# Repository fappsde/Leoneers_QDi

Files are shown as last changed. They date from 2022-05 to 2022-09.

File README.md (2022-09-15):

# Future Engineers - Leoneers_QDi - Deutschlandfinale

Dieses Repository bietet Einblicke in den Weiterentwicklungsprozess unseres autonom fahrenden Roboterautos nach unserem Vorentscheid in Dortmund, welches wir im Rahmen der Future Engineers Category der World Robot Olympiad (WRO) konzipiert und programmiert haben. 
Die unveränderte Dokumentation des Vorentscheids ist diesem [Branch](https://github.com/fappsde/Leoneers_QDi/blob/Vorentscheid_Dortmund/README.md) zu finden.

# Inhalt
  * Bilder
  * Programmcode
    * Module des Codes
    * Zusammenhang der Module und der elektromechatronischen Komponenten
    * Prozess des Erstellens, Kompilierens und Hochladens auf die Steuergeräte
  * Technische Zeichnungen
  * Video
  
# Einleitung
Wir, dass sind Felix und Philipp aus Aachen, haben seit der 5. Klasse jährlich an der WRO teilgenommen. Dementsprechend war die WRO eine Konstante in unserer Schulzeit, auf die wir uns jedes Jahr aufs neue freuten. Eigentlich wollten wir im Jahr 2020 das letzte Mal vor unserem Abitur 2021 in der Football Category antreten. Daraus wurde leider nichts. Umso größer war die Freude als wir feststellten, dass wir dieses Jahr ein aller letztes Mal die Möglichkeit haben an der WRO teilnehmen zu können. Zwar stellten wir fest, dass die Football Category, welche uns die vergangenen Jahre immer viel Spaß bereitete, nicht mehr ausgetragen wird, aber genau so spannend und interessant erschienen uns die neuen Kategorien der WRO. 
Da uns beide die Thematik der zukünftigen Mobilität und das autonome Fahren interessiert, entschieden wir uns dazu an der Future Category teilzunehmen, und ein autonomfahrendes Auto zu konzipieren.

## Anfängliche Entscheidungen

Nachdem wir die Entscheidung getroffen hatten, dass wir teilnehmen wollen, kam die Frage auf mit welchem Roboter System wir die Herausforderung des Autonomenfahrens meistern wollen? In der Vergangenheit arbeiteten wir immer gerne mit dem EV3 und Lego Technik. Jedoch stießen wir insbesondere die Programmierung betreffend mit der EV3 eigenen Programmiersprache auf Grenzen. Aus diesem Grund entschlossen wir uns dazu eine neue Herausforderung anzunehmen, und die EV3 Welt hinter uns zu lassen. Mit dieser Entscheidung dem Mindstorms Kosmos den Rücken zu zukehren, waren wir nun allerdings mit der Frage konfrontiert für welches der zahlreichen Robotersysteme, welche auf dem Markt erhältlich sind, wir uns entscheiden wollten.

Zunächst überlegten wir uns das Roboterauto von Grund auf selbst mittels CAD und additiver Herstellung zu konstruieren. Jedoch wurde uns schnell klar, dass dies zeitlich neben dem Studium leider nicht möglich gewesen wäre. Deshalb wählten wir ein altes ferngesteuertes Auto als Chassis unseres ersten Roboterautos für die Teilnahme am Vorentscheid. Als EV3 Stein Ersatz arbeiteten wir von nun an mit einem Raspberry Pi CM4. Des Weiteren verfügte das erste Auto über zwei Raspberry Pi Kameras, welche wir für das autonome Fahren und das Erkennen der Hindernisse verwendeten. Damit der Antriebs- und der Servomotor vernünftig vom Raspberry Pi angesteuert werden können, mussten wir feststellen, dass ein ESP 32 Mikrocontroller notwendig war, da das PWM (Pulsweitenmodulation) Signal ansonsten nicht konstant gewesen wäre, was ein Zittern des Servomotors verursacht hätte. Mit dieser technischen Ausstattung fuhren wir zum Vorentscheid nach Dortmund.

## Vorentscheid Dortmund

Aufgrund unserer zahlreichen Teilnahmen seit der 5. Klasse an der WRO wissen wir, dass der eigentliche Wettbewerbstag immer etwas ganz besonderes ist. Nicht nur, weil es ein schönes Ereignis in einer uns fremden Stadt ist, sondern auch, weil an diesem Tag die intensive Arbeit der letzten Wochen und Monate auf die Probe gestellt. Des Öfteren fuhren wir mit einem sehr guten Gefühl zum Wettbewerb, und mussten dann leider feststellen, dass wir uns getäuscht hatten, da der Roboter auf einmal nicht mehr das machte, was er sollte bspw. aufgrund der örtlichen Gegebenheiten, welche die Sensorik anders beeinflusst als bei der Vorbereitung. Dementsprechend lernten wir über die Jahre mit Überraschungen am Wettbewerbstag umgehen zu können. 
Ein ähnliches Erlebnis hatten wir auch bei unserem Vorentscheid in Dortmund im Juni. Zuhause und vor den Wettbewerbsdurchläufen vor Ort alles perfekt läuft. Doch dann kommt der entscheidende Durchlauf, wo unser Auto auf einmal nach der ersten Kurve an der Bande hängen blieb, was in diesem Augenblick natürlich sehr ärgerlich und frustrierend ist. Aber auch das gehört zur WRO dazu.

Dennoch hatten wir das Glück, dass wir uns als 1. Platz für das Deutschlandfinale qualifizieren konnten. Wir freuen uns sehr auf diese neue Herausforderung, denn in Dortmund stellten wir die folgenden Probleme fest, die es zu lösen galt:
 * Zu großer Wenderadius, wodurch das Auto die Kurven zu groß fuhr und auch nicht flexibel genug den Hindernissen ausweichen konnte.
 * Die Bandenerkennung, die wir mittels einer Bilderkennung implementierten, war vor Ort fehleranfällig, da das Bild der Kamera überbelichtet war, sodass  die schwarze Bande nicht mehr erkannt werden konnte. 

## Umbau des Roboterautos
Mit den in Dortmund festgestellten Problemen begann für uns zu Hause wieder die Arbeit, diese Probleme zu beheben. Dadurch, dass der Wenderadius zu groß war und auch an dem alten Modell nicht mehr vergrößert werden konnte, mussten wir um diesen zu verkleinern noch eine Hinterradlenkung einbauen. Wir entschieden uns einen zweiten Prototypen zu entwickeln, um das Auto, was bereits funktionierte auch wenn nicht perfekt, nicht zu demontieren, um so ggf. auf ein Backup zurückgreifen zu können. 

### Doppelachslenkung

Damit wir die Hinterradlenkung verbauen konnten, mussten wir zunächst die aktuelle Bodenplatte des Roboterautos neu konstruieren, um jeweils vorne und hinten eine Lenkeinheit verbauen zu können. Außerdem musste die Position des Motors geändert werden und ein weiterer Servomotor musste verbaut werden. Zunächst fertigten wir eine technische Zeichnung auf Papier an um diese anschließen in das CAM Programm zu übertragen. Dadurch, dass wir die neue Bodenplatte aus Aluminium frästen, waren diese Arbeitsschritte notwendig. 

### Elektromechanische Komponenten und Platinendesign 

Eine weitere Umbaumaßnahme ging mit dem Design einer eigenen Platine einher. Damit entstand wohl auch der optisch größte Unterschied vom neuen Modell zum alten, denn dank der Platine verschwand der auffällige Kabelbaum. Nicht nur optisch verschönert die Platine das Auto, sondern sie verfügt über jeweils zwei verbaute Rasberry Pi CM4 Module und ESP32 über mehr Rechenleistung und spart gleichzeitig noch Gewicht ein.

Beim alten Modell ist der verbaute ESP32 regelmäßig abgestürzt. Es lag die Vermutung nahe, dass das Abstürzen durch zu wenig Rechenleistung verursacht wurde, sodass das Ansteuern der Lenkung und der Beleuchtung zu viel für einen ESP war. Deshalb designten wir die Platine so, dass die Platine nun Platz für zwei ESP32 bietet. Der eine ESP übernimmt die Ansteuerung der Doppelachslenkung und der zweite ESP ist dafür gedacht die nicht unbedingt notwendigen Spielereien, wie das Bremslicht anzusteuern. So konnten wir bis dato Abstürze des ESP‘s verhindern.

In unserem alten Modell verbauten wir zwei Kameras, die jeweils einen Blickwinkel von 60 Grad, so erzielten wir einen Blickwinkel von 120 Grad. Allerdings mussten wir im Vorentscheid feststellen, dass dies insbesondere beim Vorbeifahren an den Hindernissen zu wenig war. Daher war  der nächste Schritt naheliegend eine dritte Kamera zu verbauen, um einen größeren Öffnungswinkel von 180 Grad zu erhalten. Allerdings begrenzte ein Rasberry Pi uns daran, denn an einen Rasberry Pi können lediglich nur zwei Kameras angeschlossen werden. Da für uns klar war, dass wir drei Kameras verbauen wollten, mussten wir noch einen zweiten Rasberry Pi anschließen, was in dem Design der Platine ebenfalls berücksichtigt wurde.

## Autonomes Fahren und Hinderniserkennung

Bereits vor dem Vorentscheid war unsere erste Idee, die wir für die Orientierung auf dem Spielfeld verfolgten, die Verwendung von Lidar Sensoren, welche vorne und jeweils an den Seiten des Autos verbaut wurden. Lidar Sensoren werden bereits für das autonome Fahren in Kraftfahrzeuge verbaut, da diese ein Abbild der Umgebung erzeugen können. Dadurch, dass die Lidar Sensoren mit Infrarotlicht arbeiten, stellten wir fest, dass die damaligen Lidarsensoren mit der schwarzen Bande des Spielfeldes nicht kompatibel war, weshalb wir die Idee der Lidar Sensoren verwerfen mussten.
Die Alternative auf die wir uns dann konzentrierten, war die Verwendung der Kameras. Wir verwendeten zwei Kameras. Mithilfe der Kameras gelang es uns die Banden und die Hindernisse zu erkennen. Dementsprechend fuhr die erste Version mithilfe von Bilderkennungsalgorithmen autonom.

Beim Vorentscheid wurde uns jedoch klar, dass die nur die Verwendung der Kameras auch ihre Schwächen mit sich brachte. Denn das Problem war, dass die Bande in bestimmten Situationen zu reflektierend wirkte und so auf der Kamera nicht mehr schwarz sondern weiß erschien. 
Uns war daher klar, dass wir die Problematik der Überbelichtung umgehen wollten und uns beim autonomen Fahren nicht mehr auf die Kameras verlassen wollten. Dies führte dazu, dass wir noch einmal unsere erste Idee, die Verwendung von Lidar Sensoren, aufgriffen. Dieses mal wurden wir auch nach einem Lidar Sensor fündig, der sich durch die schwarze Bande nicht beirren lässt. Statt mehreren Lidar Sensoren, die an den jeweiligen Seiten verbaut werden, dreht sich der neue Lidar permanent im Kreis, sodass wir nicht mehrere verbauen musste. 

Der schöne Vorteil an dem funktionierenden Lidar im Vergleich zu der Verwendung der Kameras, ist, dass wir so wesentlich besser die Banden erkennen können und das auch schon aus einer gewissen Distanz. Die Entfernungen, welche der Lidar misst, lassen sich anschließend in einer Karte kartographieren. Da wir bei der alten Version auch nicht wussten, wo wir uns auf dem Spielfeld befanden, haben wir noch eine Positionskamera verbaut. Die Positionskamera begegnet uns im Alltag täglich, wenn man eine Computer Maus benutzt. Die gleiche Technik machen wir uns zu Nutze, sodass mit den Winkelinformationen des Gyro Sensors und der Positionskamera die genaue Position des Autos in der Karte, die das Spielfeld darstellt eintragen können. Das ermöglicht es uns die Banden nicht anzufahren. 

Für das Erkennen der Hindernisse im Hindernisrennen ist die Verwendung der Kameras aber weiterhin notwendig, da wir die Farben ermittelt werden müssen, was der Lidar nicht kann. 

## Herausforderungen im Entwicklungsprozess

Nicht nur unser Auto muss die Hindernisse im Rennen meistern, sondern auch wir sind in der Entwicklung auf das ein oder andere Hindernis gestoßen. Aus unseren Lego Mindstorms Zeiten kannten wir es bereits uns mit unerwartet auftretenden Fehlen zu befassen, die nicht nur Zeit sondern auch Nerven kosten. So waren wir bspw. in der Wettbewerbswoche einmal an dem Punkt, dass die Kameras auf einmal nicht mehr funktionieren wollten. Dann begann eine lange Fehlersuchnacht, bis wir die Ursache, Lötzinnreste auf der Platine, die einen Kurzschluss verursachten, auffinden konnten. Ein ähnlich ärgerliches Problem ereignete sich einen Tag vor unser Abfahrt zum Wettbewerb nach Chemnitz und zwar brannte einer der Servomotoren durch. Das Problem war dann in dieser kurzen Zeit einen neuen Servo zu bekommen, den dann wieder zu verbauen und mit dem Programm in Einklang zu bringen.

Eine WRO Teilnahme ohne Harausforderungen wäre ja auch langweilig:)

# Übersicht der technischen Komponenten

* 2 x Raspberry Pi CM4
* 2 x ESP 32 Mikrocontroller
* 3 x Raspberry Pi Kamera
* Gyro Sensor
* Lidar Sensor
* Positionskamera

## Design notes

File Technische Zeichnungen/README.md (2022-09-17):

# Technische Zeichnungen

Als Chassis entschieden wir uns dazu ein altes ferngesteuertes Auto zu verweden. Um den Raspberry Pi und die anderen Komponenten mit diesem Chassis verbinden zu können, mussten wir zunächst mit CAD Halterungen erstellen, welche wir anschließend mit unserem 3D-Drucker druckten.

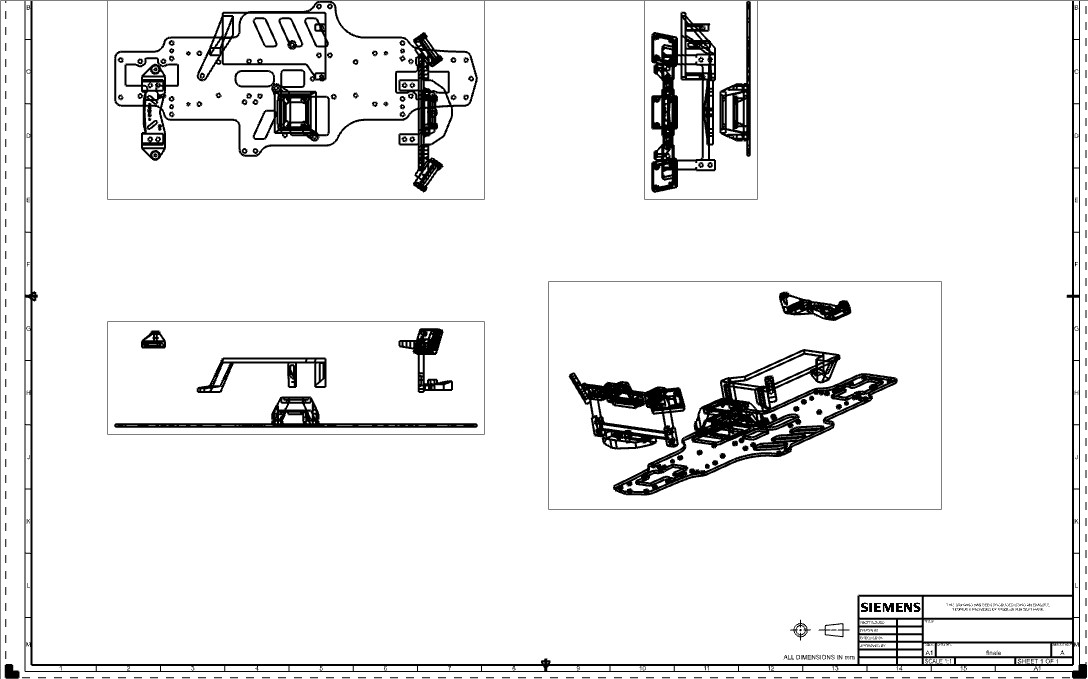
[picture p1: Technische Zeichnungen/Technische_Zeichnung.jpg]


# Schaltpläne für die Hauptplatine
Die Platine für die zweite Genration wurde von uns mit dem Programm EAGLE (Einfach Anzuwendender Grafischer Layout Editor) erstellt. Dazu haben wir zuerst alle gewünschten Komponenten gewählt und einen passenden Schaltplan mit diesen erstellt. Mit diesem Schaltplan kann man anschließend ein Layout der Komponenten erstellen, wie diese später auf der Platine platziert werden sollen. Ziel war es, auf so wenig wie möglich PLatz alle Bauteile zu platzieren. Schlussendlich war es uns möglich mit 4 Lagen und einer Größe von 20cm x 7.5cm alle Komponenten unterzubringen. Damit ist die PLatine nur knapp größer als das Raspberry Pi CM4 IO Board, welches wir in der ersten Generation verwendet haben. Dennoch ist die doppelte Rechenleistung auf dieser, inklusive ESP-23ige und Steckern, untergebracht. Für diese haben wir bei der In der ersten Generation noch eine extra Platine und viele Kabel gebraucht.

Die gesamte Entwicklung und Inbetriebnahme der Platine, sowie die dazugehörigen Aufgaben wurden ohne externe Hilfe in unserem Team durchgeführt. Die Bestückung der SMD-Bauteile wurde freundlicherweise Maschinell bei der PicoLAS-GmbH durchgeführt.
Selbes gilt auch für die Entwicklung des gefrästen Chassis.

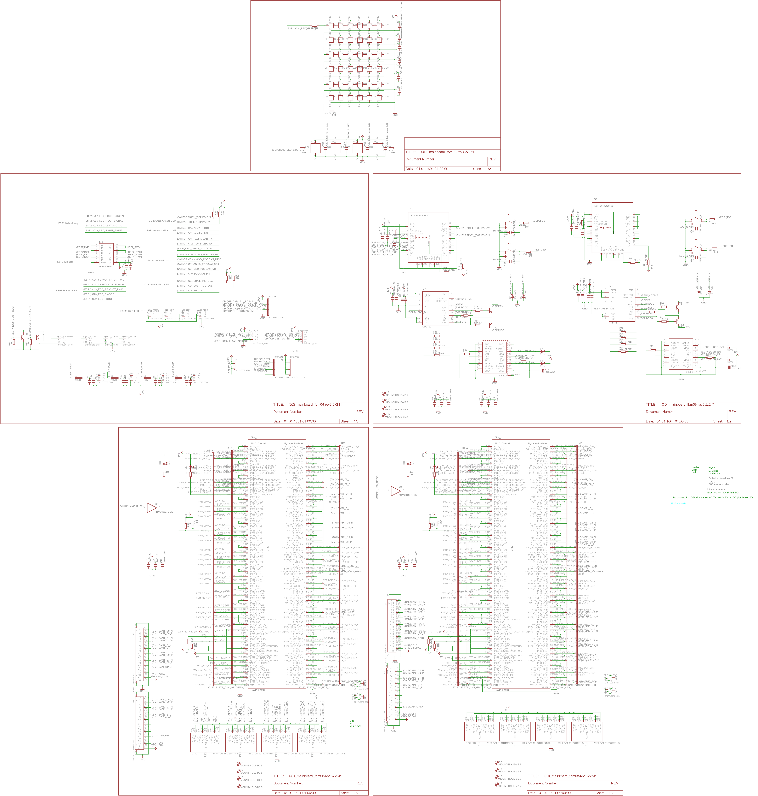
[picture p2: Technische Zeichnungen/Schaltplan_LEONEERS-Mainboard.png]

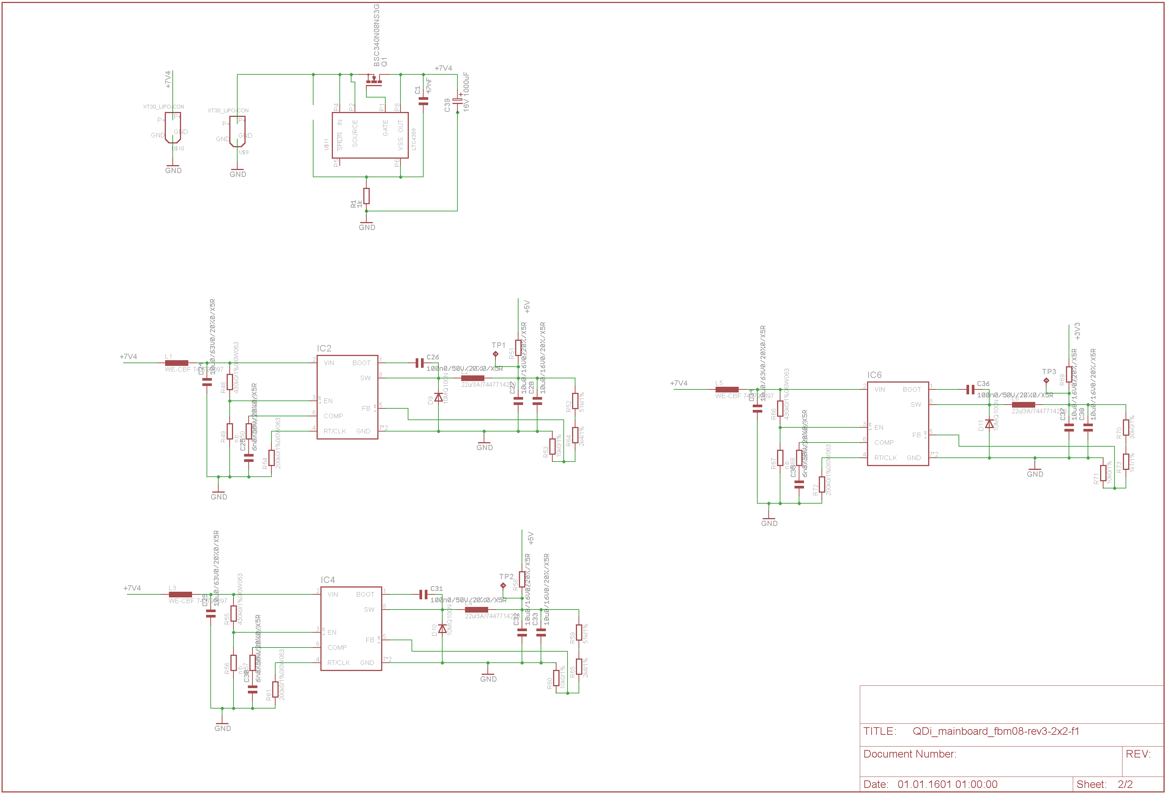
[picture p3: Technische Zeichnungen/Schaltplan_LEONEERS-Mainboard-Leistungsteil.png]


# Layout der Hauptplatine

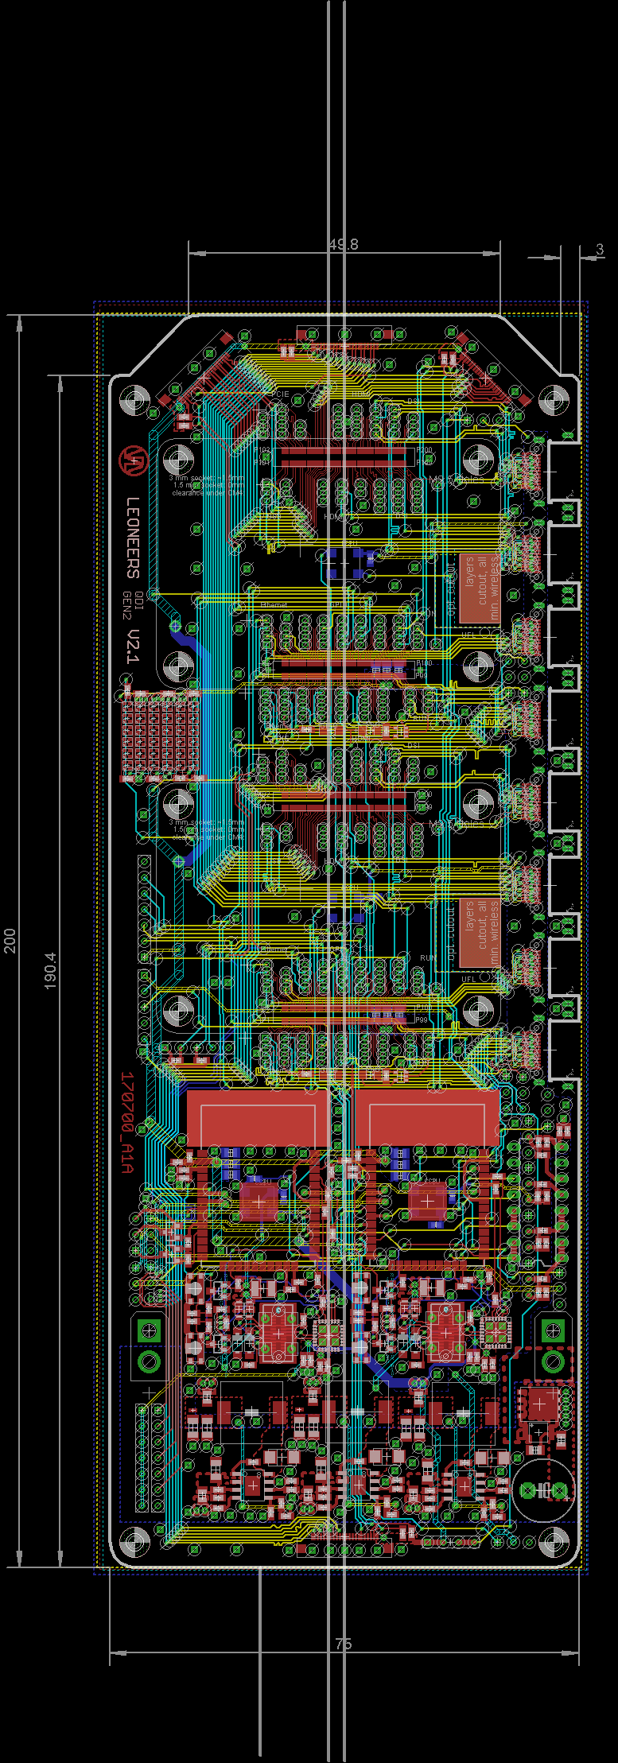
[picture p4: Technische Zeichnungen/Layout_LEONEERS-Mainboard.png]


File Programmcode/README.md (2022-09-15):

# Programmstruktur
Im Wesentlichen lässt sich unsere Programmstruktur in zwei Teile seperieren, einerseits das Programm für die ESP und andererseits die Programme der beiden Raspberry Pi's.  
Als Schnittstelle zwischen dem Antrieb des Roboterautos und dem einen dafür zuständigen Raspberry Pi fungiert ein ESP, welcher mittels Arduino programmiert wurde. Die Raspberry Pi's programmierten wir mit C und C++, da wir im Entwicklungsprozess feststellten, dass Python sich auf die Geschwindigkeit negativ ausgewirkt hätte. 

## Module des Codes

Unser Code lässt sich in mehrere Teile unterteilen, dieser verfügt unter anderem über ein Hauptprogramm. Des Weiteren über ein Programm, welches die Kameras auswertet und die Daten permanent an das Hauptprogramm übermittelt. Außerdem gibt es noch ein Programm, das den Gyro Sensor ausließt. Diese Teile waren bereits der ersten Version. Bei unserer jetzigen Version sind noch die Programmteile hinzugekommen, die den Lidar und die Positionskamera auswerten und das Kartographieren der Karte übernehmen. Das Hauptprogramm, welches auf dem Raspberry Pi läuft, dient dann dazu alle Daten zusammen fließen zu lassen und die Geschwindigkeit und Richtung des Autos vorzugeben.

## Zusammenhang der Module und der elektromechatronischen Komponenten
Damit die Motoren jedoch angesteuert werden können, übermittelt das Hauptprogramm zunächst die Informationen an den einen ESP, der dann den Antriebs- und die Servomotoren ansteuert. Dementsprechend lässt sich sagen, dass der eine ESP die Aufgabe erfüllt die Motoren anzusteuern.

## Erstellen/Kompilieren/Hochladen
Die ESP's werden über Arduino kompiliert und das Programm anschließend mittels USB hochgeladen. Auf den Raspberry Pi's werden die Programme direkt geschrieben und beim Power Up gestartet.

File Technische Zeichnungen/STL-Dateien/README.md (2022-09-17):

Hier haben wir alle STL- Dateien von den von uns erstellten 3D-Modellen gesammelt.
Auf https://1drv.ms/f/s!Ajk7HkkcY5YIkIYCL9fZXsYnURJLaA OneDrive können die Dateien als 3D Vorschau angezeigt werden.

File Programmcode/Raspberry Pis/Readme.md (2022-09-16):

Die Raspberry Pis werden mit mehreren verschiedenen Klassen gesteuert, welche jeweils einem Sensortyp bzw einer Funktionsgruppe zugeordnet sind. In der Mainloop-Klasse fließen die Daten zusammer und werden zu fahrbefehlen umgewandelt. Zudem werden hier die einzelnen Sensoren gesteuert, die jeweils gleichzeitig und asynchron laufen.

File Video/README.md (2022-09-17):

Hier gelangen Sie zu unserem [neuem Youtube Video](https://youtu.be/PLEGRZtfeYY) und hier zum [alten Youtube Video](https://youtu.be/amUso_nRZ14).

(Beim Rendern des neuen Videos ist leider am Ende ein Fehler unterlaufen)

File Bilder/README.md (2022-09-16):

Hier sehen Sie unseren Roboter
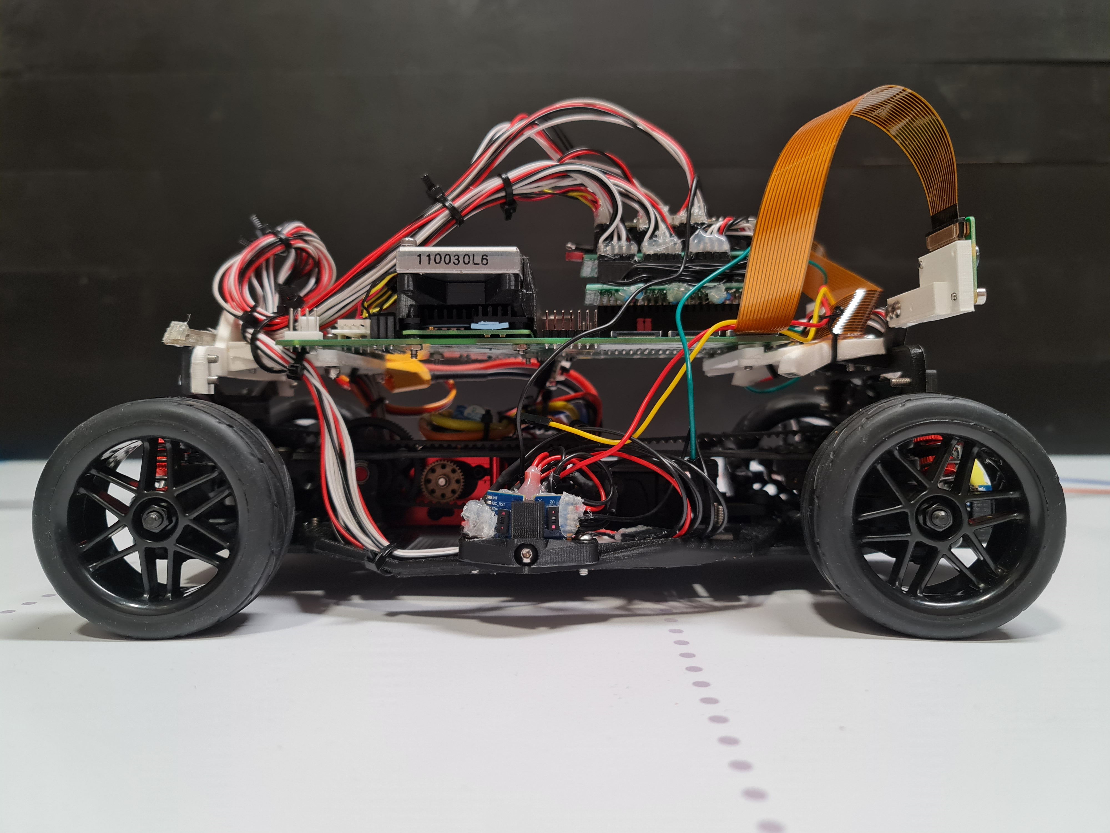
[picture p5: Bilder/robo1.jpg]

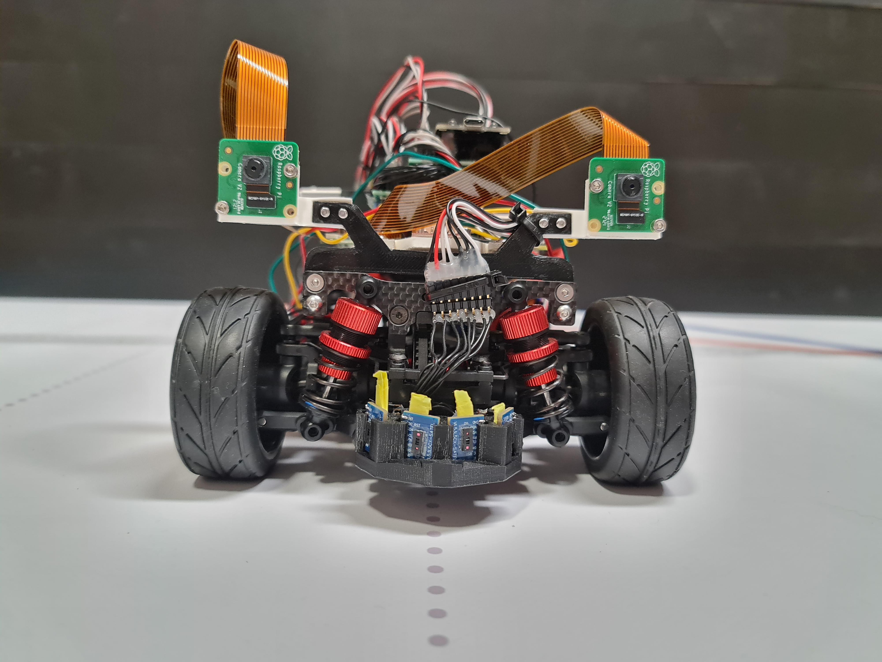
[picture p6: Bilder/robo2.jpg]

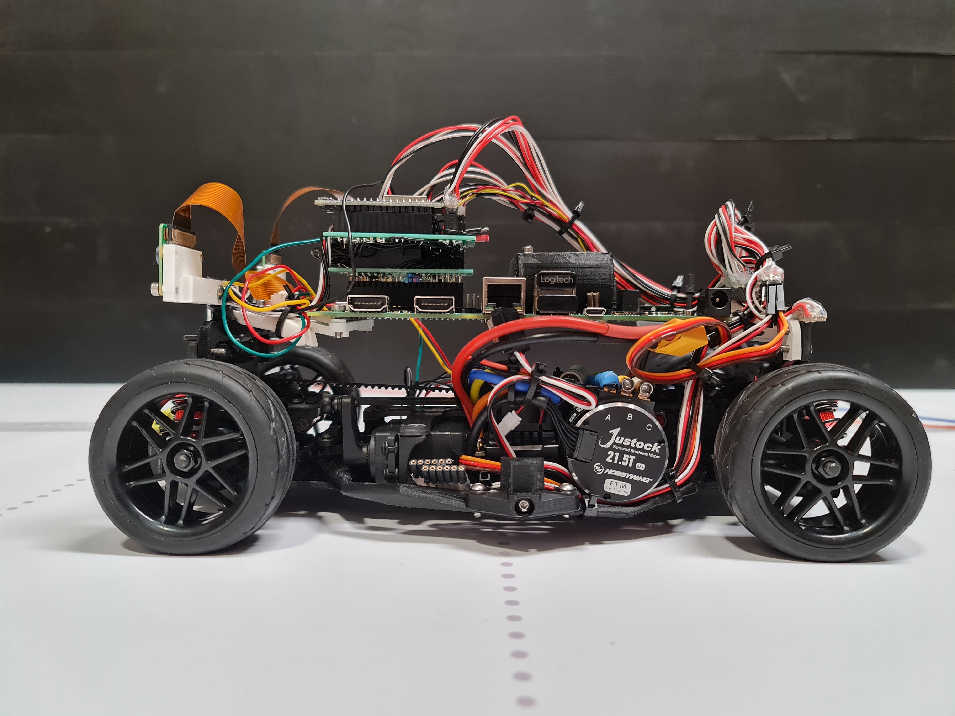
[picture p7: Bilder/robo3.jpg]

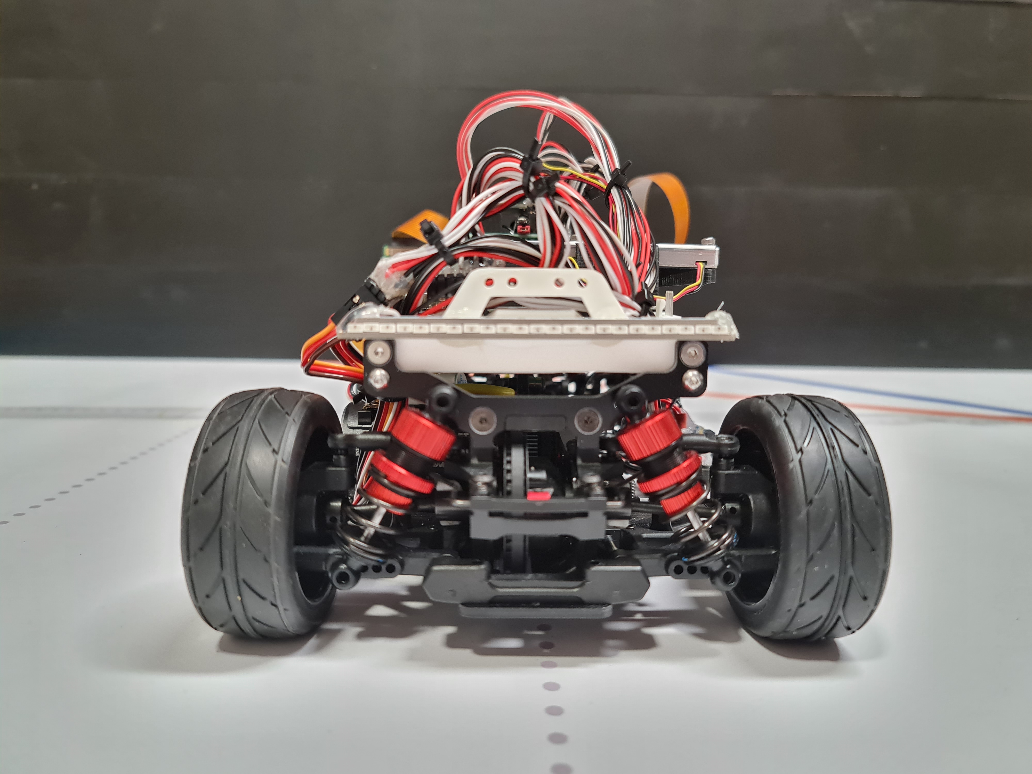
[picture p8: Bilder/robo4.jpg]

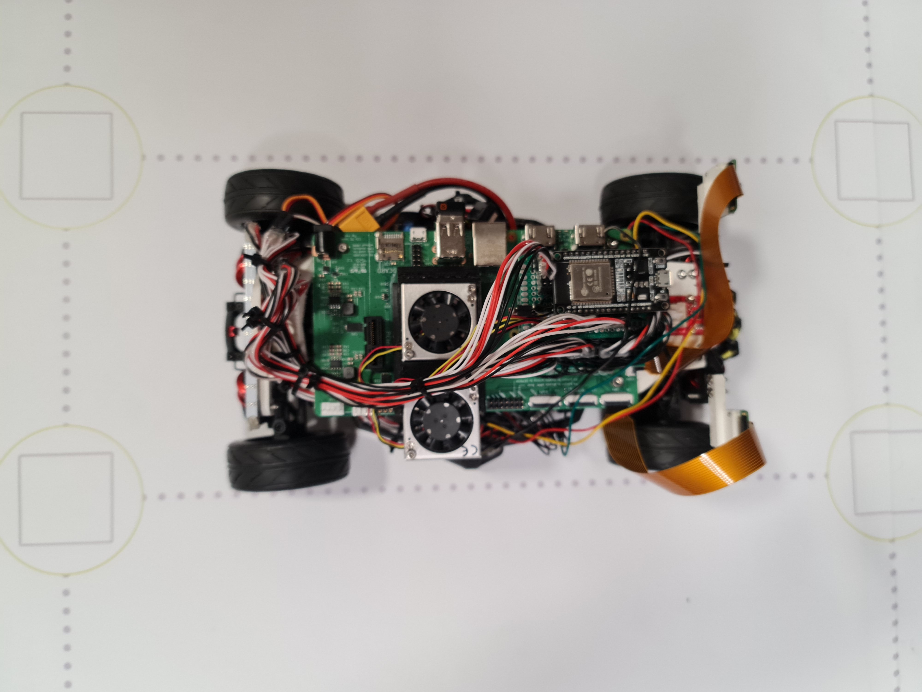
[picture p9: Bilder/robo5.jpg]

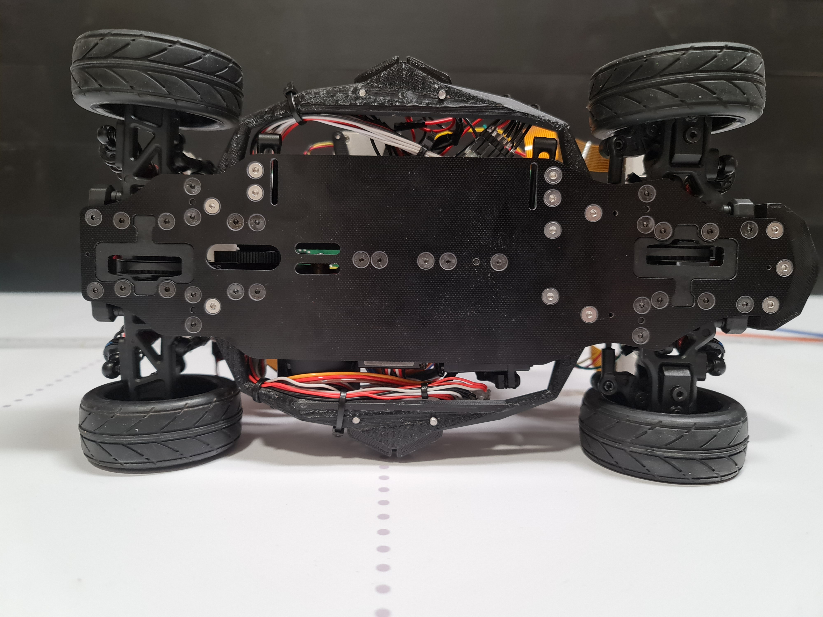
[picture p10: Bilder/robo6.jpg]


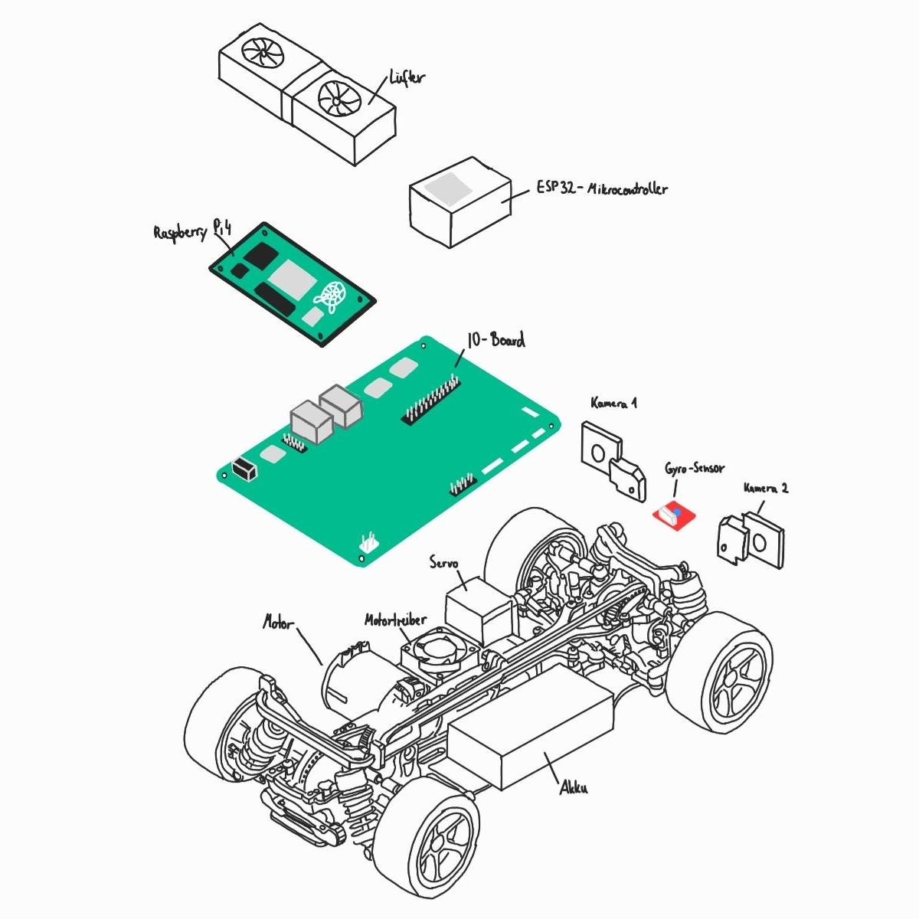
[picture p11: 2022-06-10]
Technische Zeichnungen/robo7.jpg

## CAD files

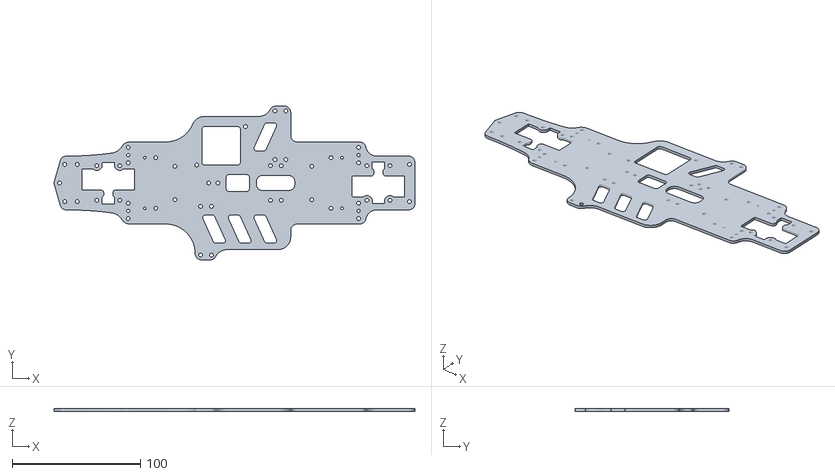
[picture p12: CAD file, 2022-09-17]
Technische Zeichnungen/STL-Dateien/chassis_tfl03_fbm04.stl
281.6 x 120.0 x 2.00

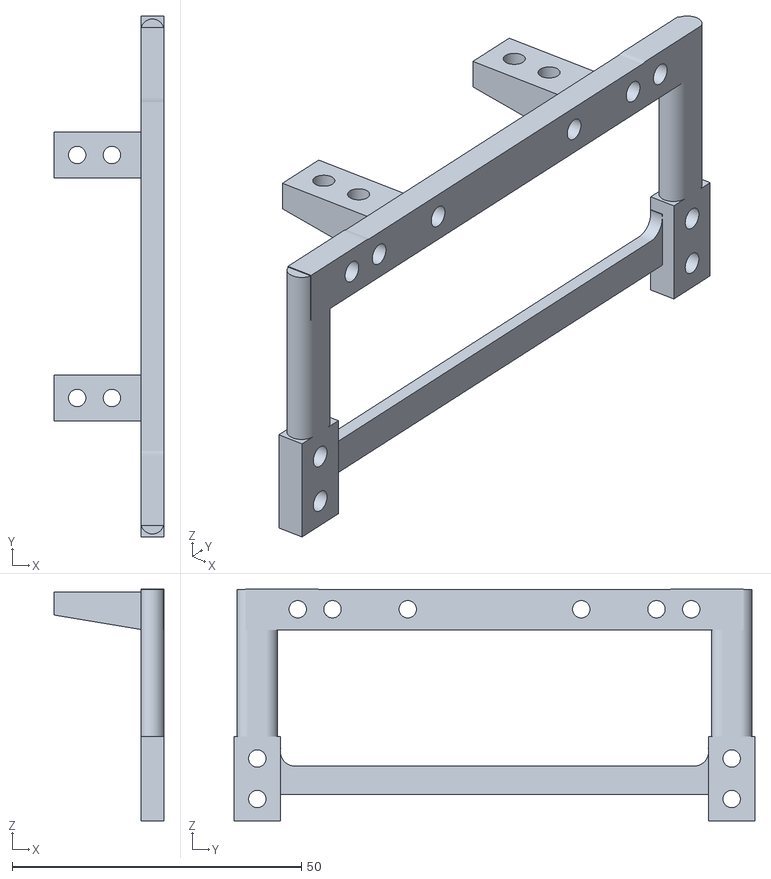
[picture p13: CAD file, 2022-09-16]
Technische Zeichnungen/STL-Dateien/cammount_gen2_front-part.stl
19.0 x 90.0 x 40.1

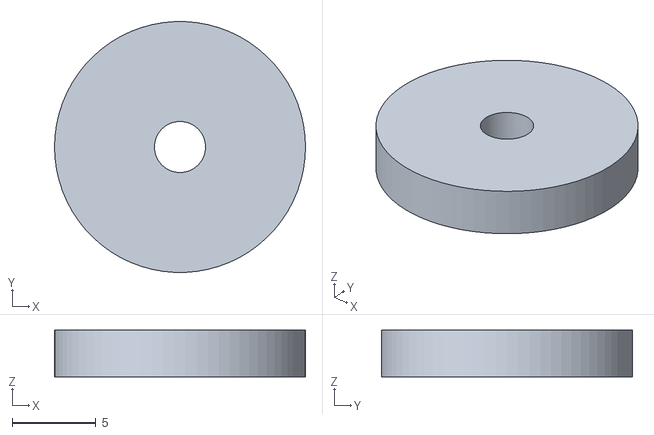
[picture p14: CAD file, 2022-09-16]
Technische Zeichnungen/STL-Dateien/gen2raspkabelhalter.stl
15.0 x 15.0 x 2.80

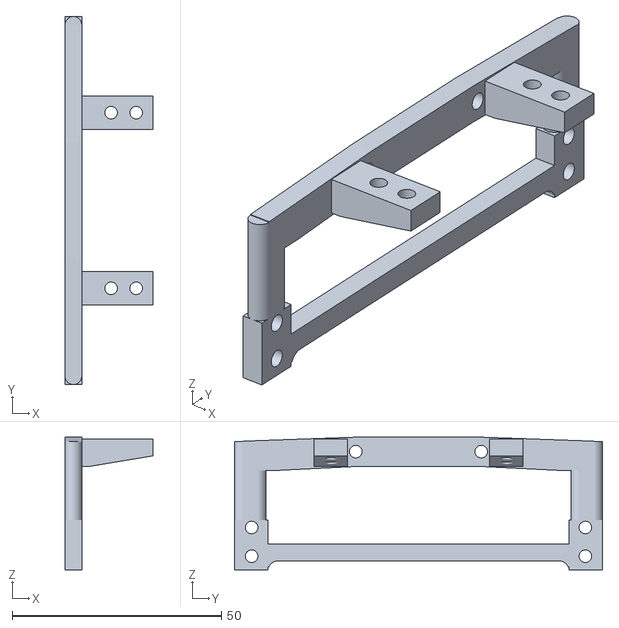
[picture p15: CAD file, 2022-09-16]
Technische Zeichnungen/STL-Dateien/cammount_gen2_rear-part.stl
21.0 x 88.0 x 31.8

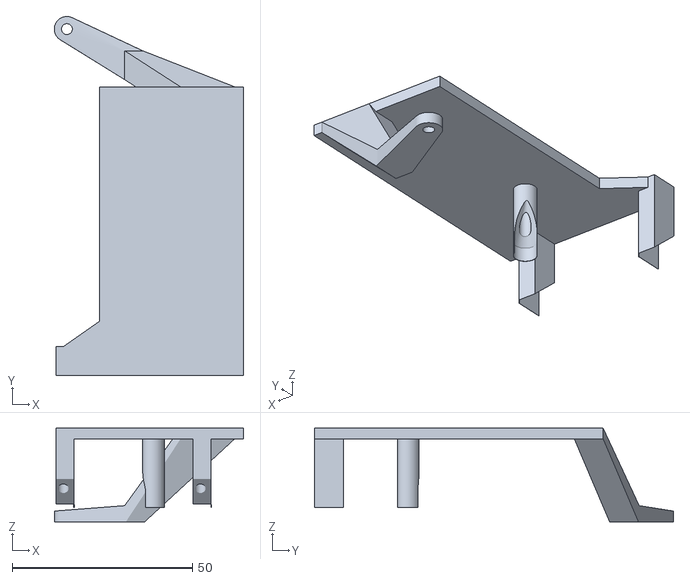
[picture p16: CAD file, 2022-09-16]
Technische Zeichnungen/STL-Dateien/lipomount.stl
52.5 x 99.5 x 26.0

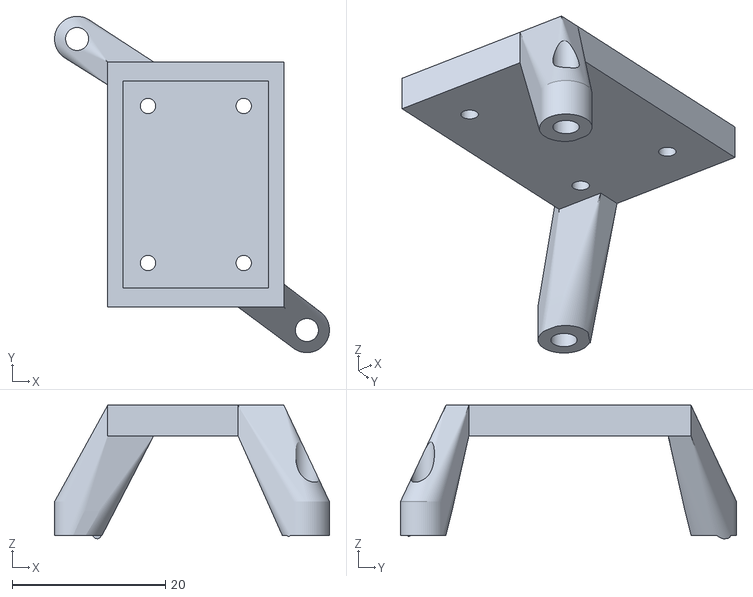
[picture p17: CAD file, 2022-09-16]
Technische Zeichnungen/STL-Dateien/poscammount2_imutop.stl
35.9 x 43.9 x 17.4

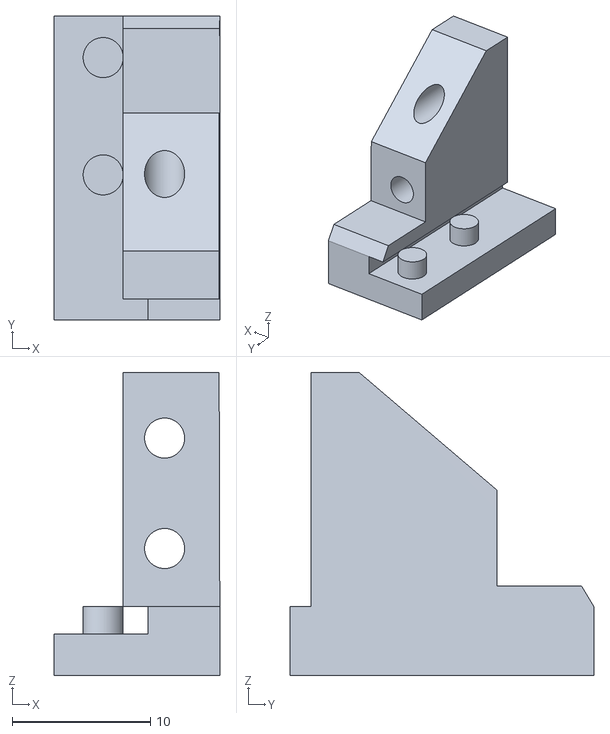
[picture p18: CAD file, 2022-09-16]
Technische Zeichnungen/STL-Dateien/Servohalter_front_anderesservo.stl
12.0 x 22.0 x 21.9

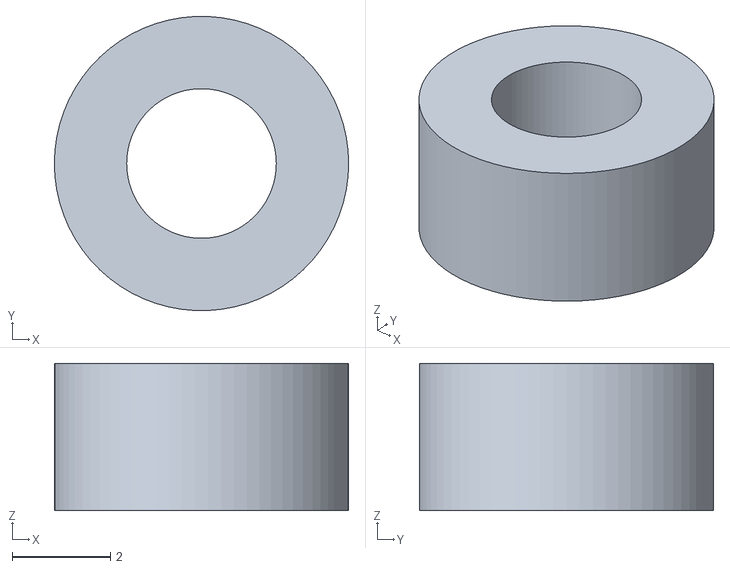
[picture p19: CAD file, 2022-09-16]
Technische Zeichnungen/STL-Dateien/gen2raspabstandshalter.stl
6.00 x 5.99 x 3.00

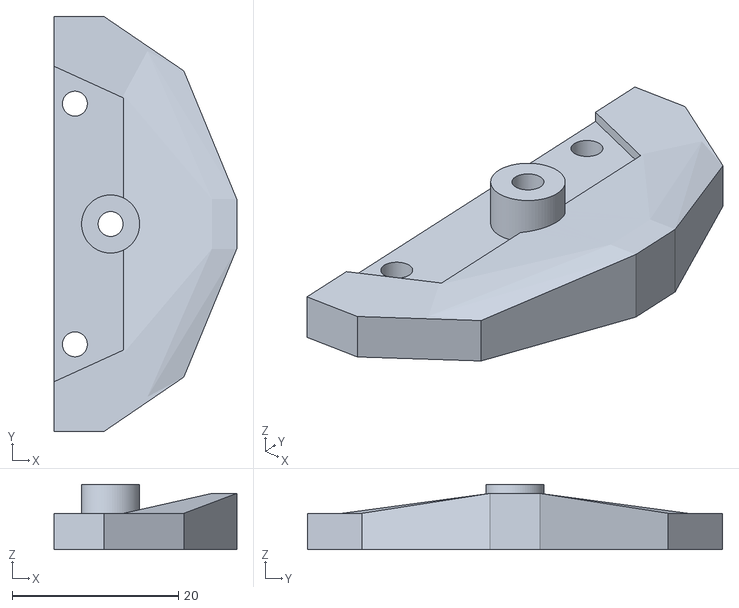
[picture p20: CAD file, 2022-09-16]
Technische Zeichnungen/STL-Dateien/frontbumper.stl
22.0 x 50.0 x 7.88

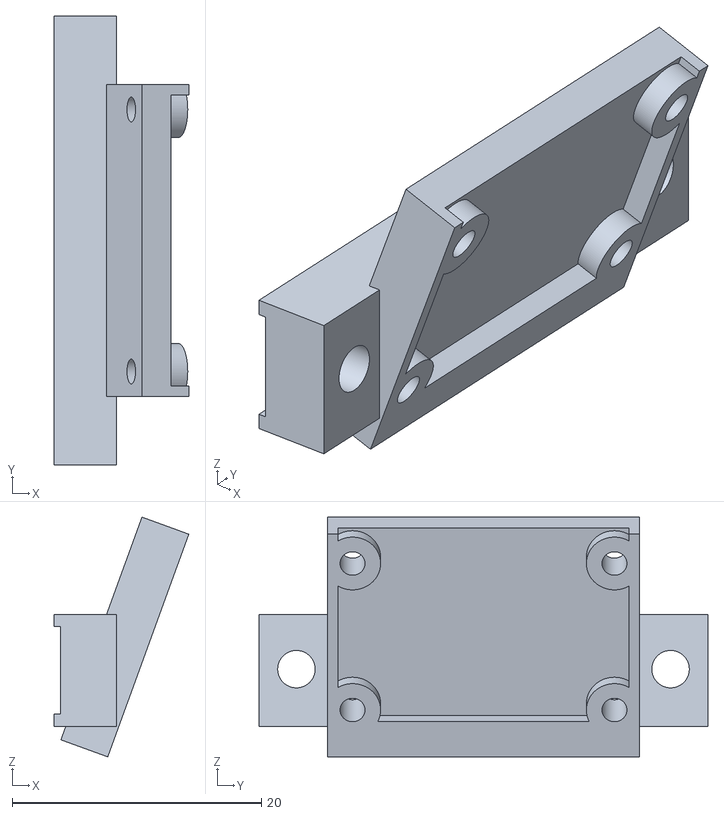
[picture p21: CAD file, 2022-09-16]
Technische Zeichnungen/STL-Dateien/cammount_gen2_frontmcam.stl
10.8 x 36.0 x 19.2

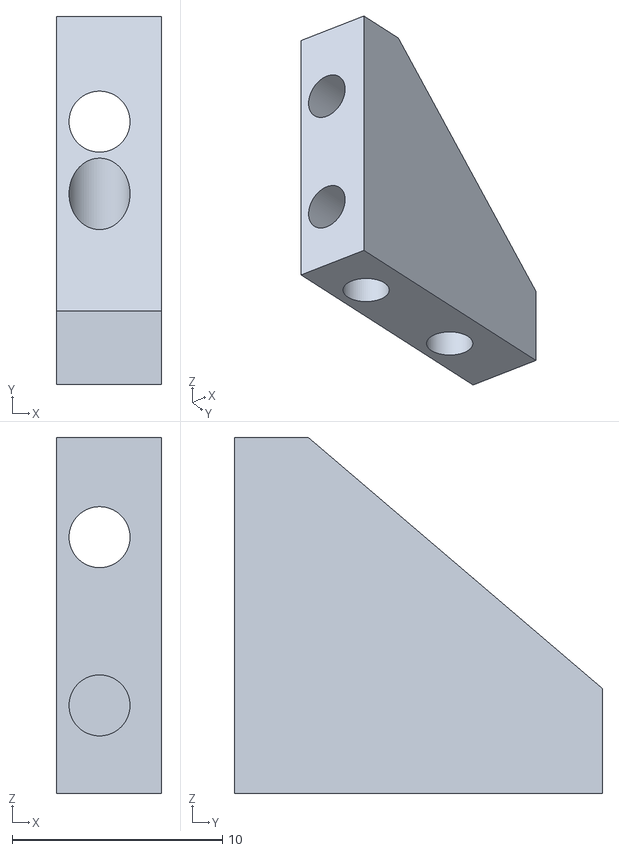
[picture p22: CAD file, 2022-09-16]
Technische Zeichnungen/STL-Dateien/Servohalter_slim.stl
5.00 x 17.5 x 16.9

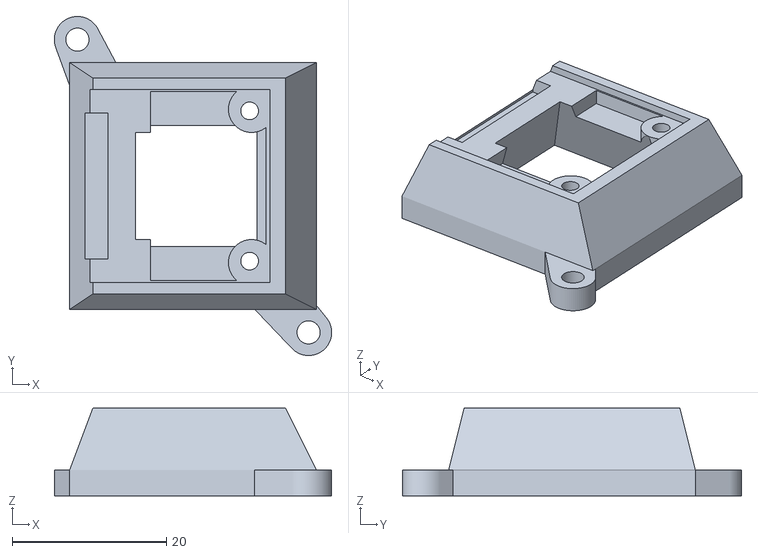
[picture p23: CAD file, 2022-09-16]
Technische Zeichnungen/STL-Dateien/poscammount2.stl
36.0 x 44.0 x 11.4

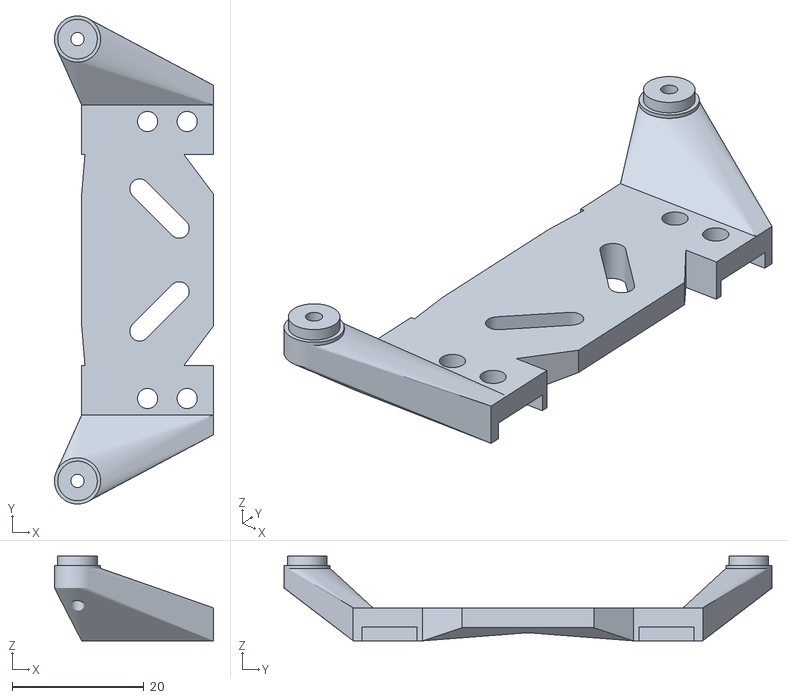
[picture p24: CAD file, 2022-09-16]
Technische Zeichnungen/STL-Dateien/cammount_gen2_front.stl
24.1 x 74.0 x 12.9

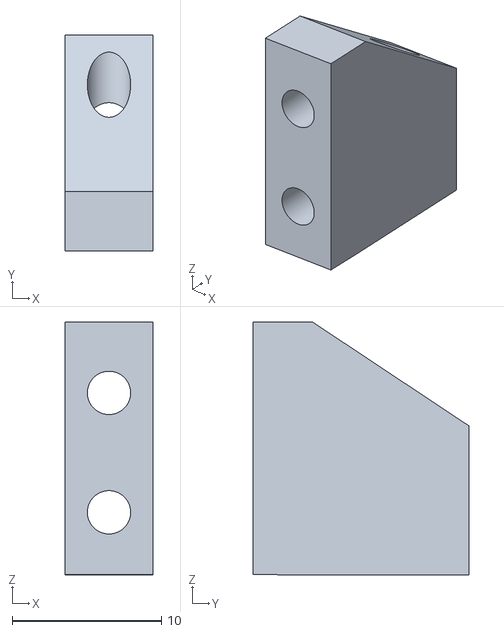
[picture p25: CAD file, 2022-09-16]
Technische Zeichnungen/STL-Dateien/Servohalter_front_short.stl
5.90 x 14.5 x 16.9

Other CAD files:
Technische Zeichnungen/STL-Dateien/cammount_gen2_frontrcam.stl
Technische Zeichnungen/STL-Dateien/tentionerv3r.stl
Technische Zeichnungen/STL-Dateien/gen2raspabstandshalter_cm-t-kh.stl
Technische Zeichnungen/STL-Dateien/Servohalter.stl
Technische Zeichnungen/STL-Dateien/Servohalter_front.stl
Technische Zeichnungen/STL-Dateien/cammount_gen2_frontlcam.stl
Technische Zeichnungen/STL-Dateien/cammount_gen2_rear.stl
Technische Zeichnungen/STL-Dateien/tentionerv3l.stl
Technische Zeichnungen/STL-Dateien/transportsicherung.stl

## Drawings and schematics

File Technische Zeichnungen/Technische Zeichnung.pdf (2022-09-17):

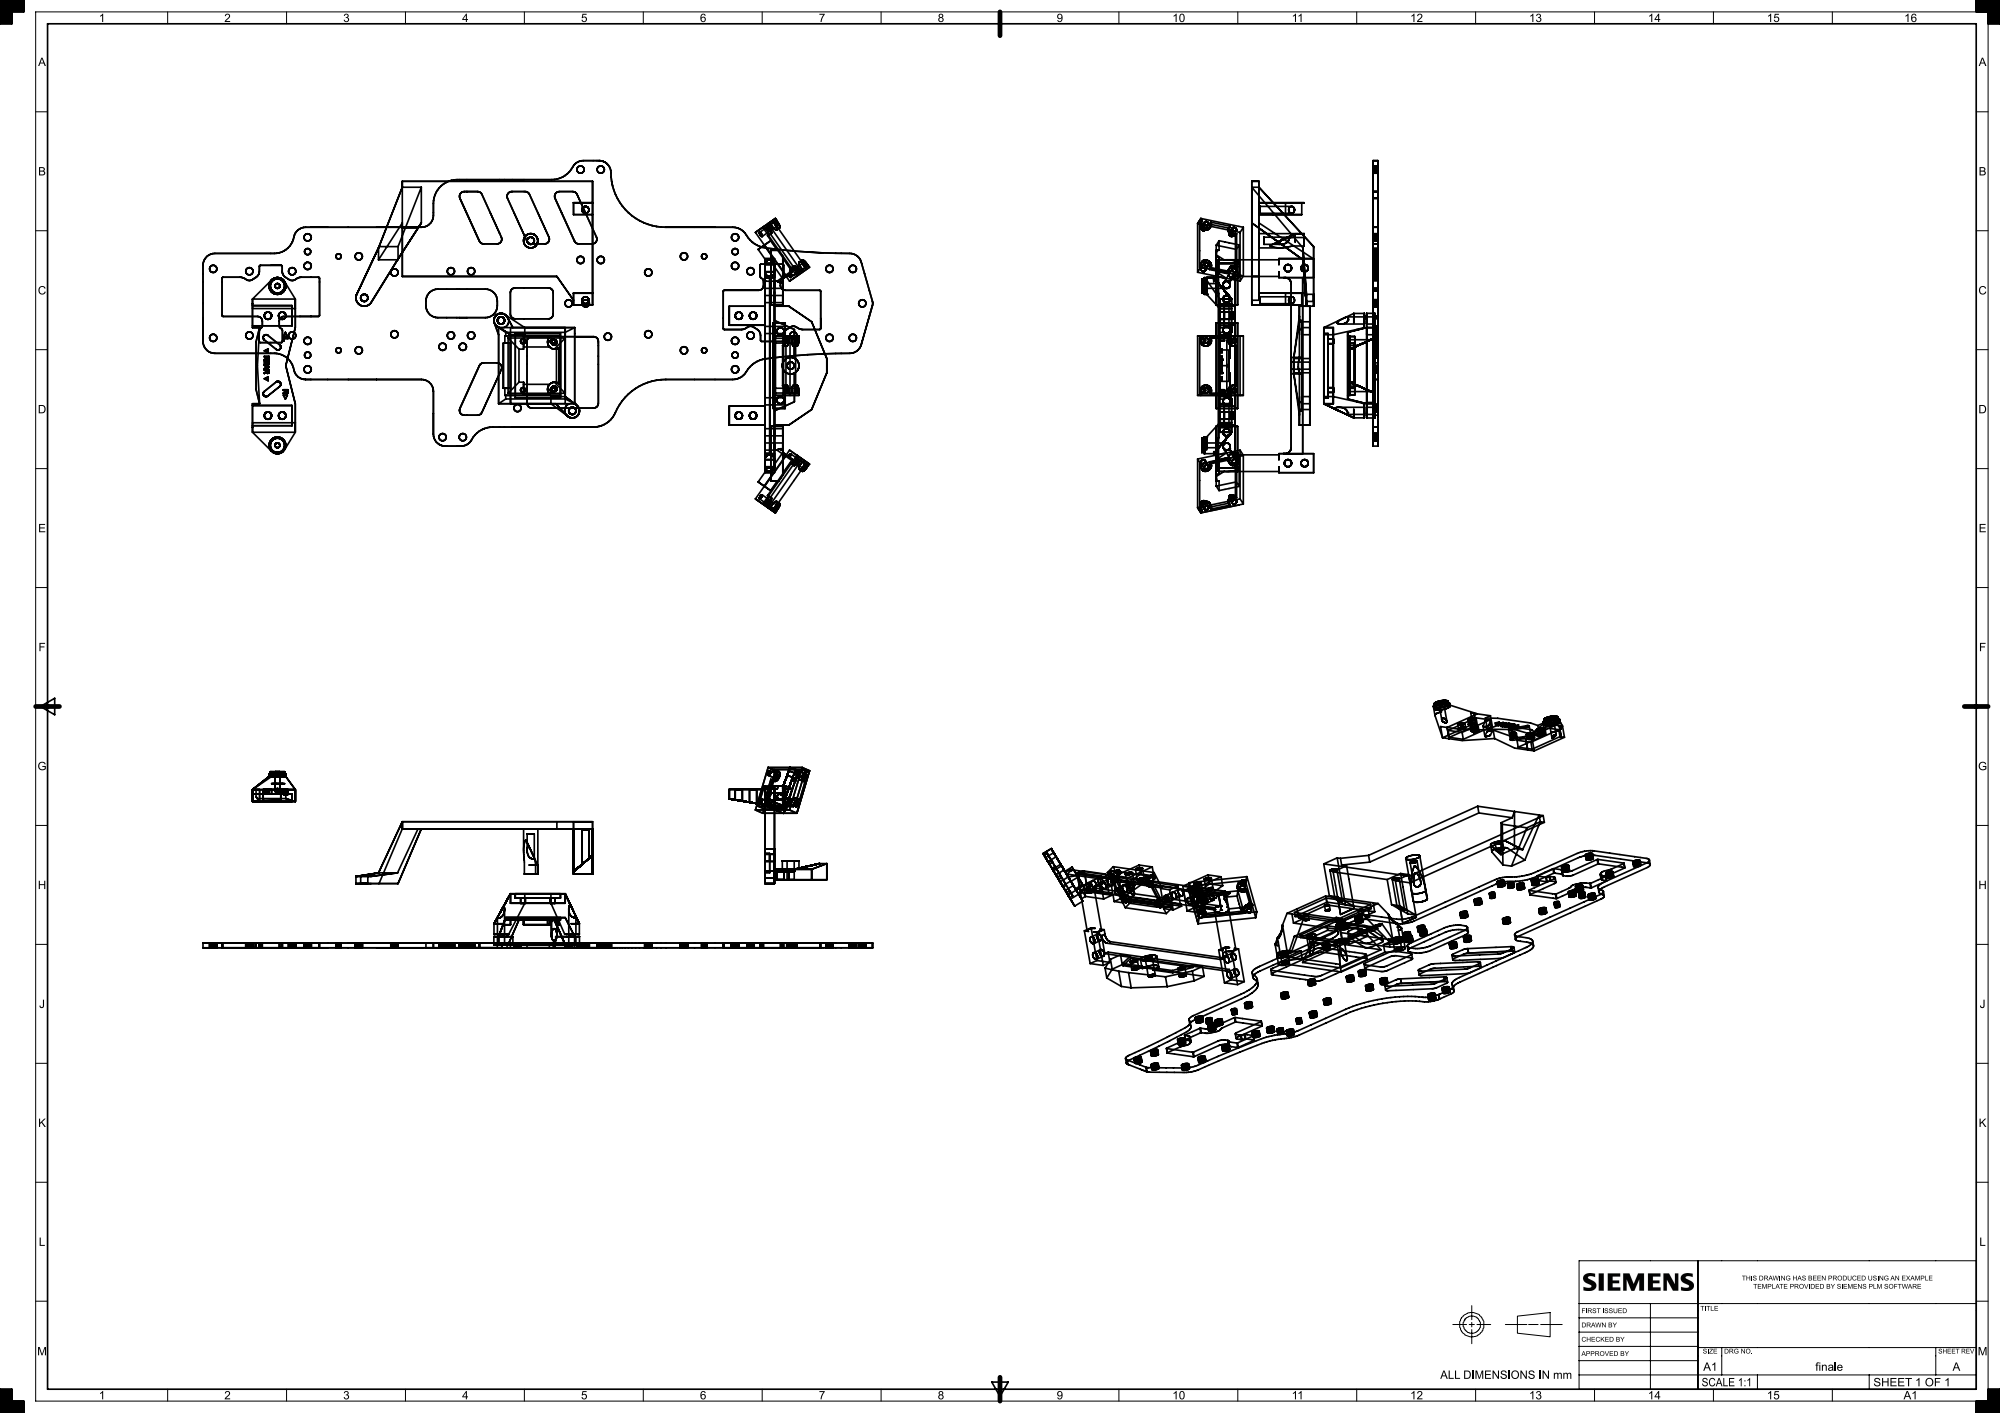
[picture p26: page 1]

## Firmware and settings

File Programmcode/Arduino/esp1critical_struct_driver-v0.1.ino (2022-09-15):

#include "Wire.h"
#include <ESP32Servo.h>
//#include <Adafruit_NeoPixel.h>
/*#ifdef __AVR__
 #include <avr/power.h> // Required for 16 MHz Adafruit Trinket
#endif*/

//Hardware pins

Servo servorear;
Servo servof;
//Servo servoR;
Servo esc;

//int SERVORPIN     5
int servorpin =5;
int SERVOFPIN =   18;
int SERVORPIN =   5;
int ESCPIN =    19;

int LIDARPIN =    33;


#define I2C_DEV_ADDR 0x55

//Drivers


//ESP32PWM servorpwm;
//ESP32PWM servofpwm;
//ESP32PWM escpwm;

ESP32PWM lidarpwm;



//Configuration


int speedlimiter=15;//1-90
int speedlimiterrev=-50;//1-90
int lenkunglimiter=90;//1-90

float servorpos = 0; 
float servofpos = 0; 
float escpos = 0; 

uint32_t i = 0;

int systemstatus=-1;//-1 unknown, 0 raspi off, 1 all systems work properly, 255 error dont start, 100 cam0 error, 101 cam1 error, 200 imu error, 201 start imu
int drivesystemidlestatus=-1;//-1 unknown, 0 raspi off, 1 driving, 5 wait for start idle,  201 imu start

//Software 


int drivespeed=0;
int nextdrivespeed=0;

long stepstonextdrivespeed=1L;
long stepstonextlenkung_rear=1L;
long stepstonextlenkung_front=1L;
long lastmillisspeed = 0L;
long lastmillislenkung_rear = 0L;
long lastmillislenkung_front = 0L;


int revint=0;//0normale 1 intiing, 2 reverse

int lidarfreq = 100;
float lidarspeed = 0.0;

int drivemode=0;//0:idle, 1:drivefwrd, 2:break, 3:breakhard, 99:disabeld, -1:drivereverse, -2:reversebreak
//int prevdrivemode=0;
int lenkung_front=0;//0:geradeaus, -: links, +:rechts
int nextlenkung_front=0;
int lenkung_rear=0;//0:geradeaus, -: links, +:rechts
int nextlenkung_rear=0;




int breakhelpmod=0;

boolean fullyinitialized=false;

void setup() {

  Serial.begin(115200);
  
  ESP32PWM::allocateTimer(0);
  ESP32PWM::allocateTimer(1);
  ESP32PWM::allocateTimer(2);
  ESP32PWM::allocateTimer(3);
  
  
  

//startsequence();

  esc.setPeriodHertz(50);    // standard 50 hz servo
  esc.attach(ESCPIN, 1000, 2000);
  servorear.setPeriodHertz(50);    // standard 50 hz servo
  servorear.attach(servorpin, 1180, 1780);// attaches the servo on pin 18 to the servo object using default min/max of 1000us and 2000us
  servof.setPeriodHertz(50);    // standard 50 hz servo
  servof.attach(SERVOFPIN, 1050, 1590);
  //Values for original servo:  1050, 1590
  
  // attaches the servo on pin 18 to the servo object using default min/max of 1000us and 2000us
  //servoR.setPeriodHertz(50);    // standard 50 hz servo
  //servoR.attach(SERVORPIN, 1050, 1590);
  // different servos may require different min/max settings for an accurate 0 to 180 sweep
  
  servorear.write(90);
  servof.write(90);
  //servoR.write(90);
  esc.write(90);


  Wire.onReceive(onReceive);
  Wire.onRequest(onRequest);
  Wire.begin((uint8_t)I2C_DEV_ADDR);
  #if CONFIG_IDF_TARGET_ESP32
    char message[64];
    snprintf(message, 64, "%u Packets.", i++);
    Wire.slaveWrite((uint8_t *)message, strlen(message));
  #endif

  lidarpwm.attachPin(LIDARPIN, lidarfreq, 10);// 1KHz 8 bit

  
  lidarpwm.adjustFrequency(lidarfreq, lidarspeed);

  pinMode(34, INPUT);//frontled
  pinMode(35, INPUT);//sonstwas
}

void loop() {
  // put your main code here, to run repeatedly:

  
  


  if(millis() > stepstonextdrivespeed + lastmillisspeed){
    lastmillisspeed=millis();
    if(nextdrivespeed<=2&&nextdrivespeed>=-2){
      nextdrivespeed=0;
    }
    if(drivespeed<nextdrivespeed){
      drivespeed=drivespeed+1;
    }else if(drivespeed>nextdrivespeed){
      drivespeed=drivespeed-1;
    }else{
      stepstonextdrivespeed=1;
    }
  }
  if(millis() > stepstonextlenkung_front + lastmillislenkung_front){
    lastmillislenkung_front=millis();
    if(lenkung_front<nextlenkung_front){
      int add=(nextlenkung_front-lenkung_front)/10;
      lenkung_front=lenkung_front+1+add;
      //dobreak(&rearstrip,0);
      
    }else if(lenkung_front>nextlenkung_front){
      int add=(lenkung_front-nextlenkung_front)/10;
      lenkung_front=lenkung_front-1-add;
      
      //dobreak(&rearstrip,1);
    }else{
      stepstonextlenkung_front=1;
      
    }
   
  }
  if(millis() > stepstonextlenkung_rear + lastmillislenkung_rear){
    lastmillislenkung_rear=millis();
    if(lenkung_rear<nextlenkung_rear){
      int add=(nextlenkung_rear-lenkung_rear)/10;
      lenkung_rear=lenkung_rear+1+add;
      //dobreak(&rearstrip,0);
      
    }else if(lenkung_rear>nextlenkung_rear){
      int add=(lenkung_rear-nextlenkung_rear)/10;
      lenkung_rear=lenkung_rear-1-add;
      
      //dobreak(&rearstrip,1);
    }else{
      stepstonextlenkung_rear=1;
      
    }
   
  }
  
  
  updatepwm();

  

  //onupdate();

delay(2);//5
}






int checkrange(int value, int minv, int maxv){
  if(value>maxv){
    return maxv;
  }
  if(value<minv){
    return minv;
  }
  return value;
}

void updatepwm(){
  if(drivemode>=0){
    esc.write(checkrange(drivespeed,-90,speedlimiter)+90);
  }else{
    if(revint!=1){
      esc.write(checkrange(drivespeed,speedlimiterrev,speedlimiter)+90);//speedlimiterrev
    }
  }
  servof.write(checkrange(lenkung_front,-lenkunglimiter,lenkunglimiter)+95);
 // servoR.write(checkrange(lenkung,-lenkunglimiter,lenkunglimiter)+95);
  servorear.write((checkrange(lenkung_rear*-1,-lenkunglimiter,lenkunglimiter)+95));

 
  
}
//Driving 
/*
void setdriveSpeed(){

  
}

void break(int steps,int delayt){
  
}

void onupdate(){
  
  
  }
*/





void displaysystemstatus(){
  systemstatus;//-1 unknown, 0 raspi off, 1 all systems work properly, 255 error dont start, 100 cam0 error, 101 cam1 error, 200 imu error, 201 start imu
  drivesystemidlestatus;//-1 unknown, 0 raspi off, 1 driving, 5 wait for start idle,6 finised  201 imu start
  

  bool unknown=false;
  
  
  


  
  
}

void startsequence(){
 
  
  
}

void startreverse(){
  revint=1;
  for(int i=95;i>40;i--){
    esc.write(i);
    delay(1);
  }
  delay(800);
  for(int i=40;i<95;i++){
    esc.write(i);
    delay(1);
  }
  delay(800);
  for(int i=95;i>50;i--){
    esc.write(i);
    delay(1);
  }

  delay(300);
  revint=2;

  
}

void onRequest(){
  Wire.print(i++);
  Wire.print(" Packets.");
  Serial.println("onRequest");
}

void onReceive(int len){
  //Serial.printf("onReceive[%d]: ", len);
  String bufferstring="";
  uint8_t buff;
  int pos=0;
  while(Wire.available()){
    
     buff=Wire.read();
     pos++;
     
    //size_t bufflen = sizeof(buff);
    //strncat( bufferstring, buff, bufflen );
     // 'str' is now a string
    //Serial.write(buff);
    bufferstring+=(char) buff;
    //Serial.println(bufferstring);
    
    
    }
    String bufstring=String(bufferstring);
    bufstring.trim();
    
    
   // Serial.println(bufferstring+bufstring+bufferstring.charAt(1)+bufstring.indexOf("spd:",1)+bufstring.startsWith("spd:")+bufferstring.length());
    //Serial.println(bufferstring.charAt(1));
    //Serial.println(bufferstring+bufstring+bufstring.indexOf("drcn:",1)+bufstring.startsWith("drcn:")+bufferstring.length());
    
    
    if(bufstring.indexOf("spd:",1)!=-1){//Geschwindigkeit
      //Serial.println("Speed");
      if(bufstring.indexOf(";",1)>bufstring.length()-2){
        String newspeed=bufstring.substring(bufstring.indexOf("sdp:",1)+7,bufstring.indexOf(",",1));
        String nextspint=newspeed;
        nextdrivespeed=checkrange(nextspint.toInt(),-90,90);
        String timetospeed=bufstring.substring(bufstring.indexOf(",",1)+1,bufstring.indexOf(";",1));

        String nextttsint=timetospeed;
        stepstonextdrivespeed=checkrange(nextttsint.toInt(),-90,90);
       // Serial.println(stepstonextdrivespeed);
        
      }
      
    }else if(bufstring.indexOf("drcn:",1)!=-1){//Lenkung
      if(bufstring.indexOf(";",1)>bufstring.length()-2){
        String pnewlenkung=bufstring.substring(bufstring.indexOf("drcn:",1)+5,bufstring.indexOf(",",1));
        String ptimetolenkung=bufstring.substring(bufstring.indexOf(",",1)+1,bufstring.indexOf(";",1));
        
        String nextlint=pnewlenkung;
        nextlenkung_front=checkrange(nextlint.toInt(),-90,90);
        nextlenkung_rear=checkrange(nextlint.toInt(),-90,90);
        
        String nextttlint=ptimetolenkung;
        stepstonextlenkung_front=checkrange(nextttlint.toInt(),-90,90);
        stepstonextlenkung_rear=checkrange(nextttlint.toInt(),-90,90);
       // Serial.println(nextlenkung);
        
      }
    }else if(bufstring.indexOf("frontdrcn:",1)!=-1){//Lenkung
      if(bufstring.indexOf(";",1)>bufstring.length()-2){
        String pnewlenkung=bufstring.substring(bufstring.indexOf("frontdrcn:",1)+10,bufstring.indexOf(",",1));
        String ptimetolenkung=bufstring.substring(bufstring.indexOf(",",1)+1,bufstring.indexOf(";",1));
        
        String nextlint=pnewlenkung;
        nextlenkung_front=checkrange(nextlint.toInt(),-90,90);
       
        
        String nextttlint=ptimetolenkung;
        stepstonextlenkung_front=checkrange(nextttlint.toInt(),-90,90);
        
      }
    }else if(bufstring.indexOf("reardrcn:",1)!=-1){//Lenkung
      if(bufstring.indexOf(";",1)>bufstring.length()-2){
        String pnewlenkung=bufstring.substring(bufstring.indexOf("reardrcn:",1)+9,bufstring.indexOf(",",1));
        String ptimetolenkung=bufstring.substring(bufstring.indexOf(",",1)+1,bufstring.indexOf(";",1));
        
        String nextlint=pnewlenkung;
        nextlenkung_rear=checkrange(nextlint.toInt(),-90,90);
       
        
        String nextttlint=ptimetolenkung;
        stepstonextlenkung_rear=checkrange(nextttlint.toInt(),-90,90);
        
      }
    }else if(bufstring.indexOf("drvm:",1)!=-1){//Fahrmodus  //0:idle, 1:drivefwrd, 2:break, 3:breakhard, 99:disabeld, -1:drivereverse, -2:reversebreak
      if(bufstring.indexOf(";",1)>bufstring.length()-2){
        String pdrvmd=bufstring.substring(bufstring.indexOf("drvm:",1)+5,bufstring.indexOf(",",1));
        String p=bufstring.substring(bufstring.indexOf(",",1)+1,bufstring.indexOf(";",1));
        
        String drvmdstr=pdrvmd;
        int ndrvmd=drvmdstr.toInt();
        if(ndrvmd==-1&&drivemode>=0){
            //start reverse
            drivemode=ndrvmd;
          startreverse();
          Serial.println("startrev");
        }
        
        drivemode=ndrvmd;
        
        
       // String nextttlint=ptimetolenkung;
        //stepstonextlenkung=checkrange(nextttlint.toInt(),-90,90);
       // Serial.println(nextlenkung);
        
      }
    }else if(bufstring.indexOf("lidar:",1)!=-1){//Lidar speed 0-100
      if(bufstring.indexOf(";",1)>bufstring.length()-2){
        String plidspd=bufstring.substring(bufstring.indexOf("lidar:",1)+6,bufstring.indexOf(",",1));
        String p=bufstring.substring(bufstring.indexOf(",",1)+1,bufstring.indexOf(";",1));
        
        String lidspdstr=plidspd;
        lidarspeed=lidspdstr.toInt()/100;
        
        lidarpwm.adjustFrequency(lidarfreq, lidarspeed);
            
          Serial.println("lidarset");
               
      }
    }else if(bufstring.indexOf("stp:",1)!=-1){//full stop
      
    }
  else if(bufstring.indexOf("sysstat:",1)!=-1){//Lenkung
      if(bufstring.indexOf(";",1)>bufstring.length()-2){
        
        String sysstat=bufstring.substring(bufstring.indexOf("sysstat:",1)+8,bufstring.indexOf(",",1));
        String drivstat=bufstring.substring(bufstring.indexOf(",",1)+1,bufstring.indexOf(";",1));
        //Serial.print(dimside);
        String sysstatstr=sysstat;
        int sysstatint=sysstatstr.toInt();
        
        String drivstatstr=drivstat;
        int drivstatint=drivstatstr.toInt();
        
        systemstatus=sysstatint;//-1 unknown, 0 raspi off, 1 all systems work properly, 255 error dont start, 100 cam0 error, 101 cam1 error, 200 imu error, 201 start imu
        drivesystemidlestatus=drivstatint;//-1 unknown, 0 raspi off, 1 driving, 5 wait for start idle,  201 imu start
        displaysystemstatus();
     }
  }
  //Serial.println();
}

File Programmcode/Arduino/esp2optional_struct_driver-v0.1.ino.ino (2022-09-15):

#include "Wire.h"
#include <ESP32Servo.h>
#include <Adafruit_NeoPixel.h>
#ifdef __AVR__
 #include <avr/power.h> // Required for 16 MHz Adafruit Trinket
#endif

//Hardware pins
#define LED_FRONT_PIN     27
#define LED_REAR_PIN     26
#define LED_INDI_PIN     25

#define lufESPPIN     15
#define luf1PIN     2
#define luf2PIN     4


#define LED_FRONT_COUNT  37
//37
#define LED_REAR_COUNT  23
#define LED_INDI_COUNT  22
#define BRIGHTNESS 50
#define LED_FRONT_BRIGHTNESS 150
#define LED_INDI_BRIGHTNESS 50

#define I2C_DEV_ADDR 0x56


#define LED_INDIINSID_PIN     12
#define LED_INDIINSID_COUNT  4
#define LED_INDIINSID_BRIGHTNESS 100
Adafruit_NeoPixel indiindsstrip(LED_INDIINSID_COUNT, LED_INDIINSID_PIN, NEO_GRBW + NEO_KHZ800);

//Drivers
Adafruit_NeoPixel frontstrip(LED_FRONT_COUNT, LED_FRONT_PIN, NEO_GRB + NEO_KHZ800);
Adafruit_NeoPixel rearstrip(LED_REAR_COUNT, LED_REAR_PIN, NEO_GRB + NEO_KHZ800);
Adafruit_NeoPixel indistrip(LED_INDI_COUNT, LED_INDI_PIN, NEO_GRB + NEO_KHZ800);



ESP32PWM lufesppwm;
ESP32PWM luf1pwm;
ESP32PWM luf2pwm;

//Configuration
int lufespfreq = 100;
int luf1freq = 100;
int luf2freq = 100;

int speedlimiter=15;//1-90
int speedlimiterrev=-50;//1-90
int lenkunglimiter=90;//1-90

float servopos = 0; 
float escpos = 0; 

uint32_t i = 0;

int systemstatus=-1;//-1 unknown, 0 raspi off, 1 all systems work properly, 255 error dont start, 100 cam0 error, 101 cam1 error, 200 imu error, 201 start imu
int drivesystemidlestatus=-1;//-1 unknown, 0 raspi off, 1 driving, 5 wait for start idle,  201 imu start

//Software 
boolean rechtsblinken=false;
boolean linksblinken=false;

int drivespeed=0;
int nextdrivespeed=0;

long stepstonextdrivespeed=1L;
long stepstonextlenkung=1L;
long lastmillisspeed = 0L;
long lastmillislenkung = 0L;
long ledmilli=0L;

int revint=0;//0normale 1 intiing, 2 reverse



int drivemode=0;//0:idle, 1:drivefwrd, 2:break, 3:breakhard, 99:disabeld, -1:drivereverse, -2:reversebreak
//int prevdrivemode=0;
int lenkung=0;//0:geradeaus, -: links, +:rechts
int nextlenkung=0;

float lufespspeed = 0;//0-1
float luf1speed = 1.5;
float luf2speed = 1.5;


int lblinkstep=0;
int rblinkstep=0;

int breakhelpmod=0;

boolean fullyinitialized=false;

void setup() {
  ESP32PWM::allocateTimer(0);
  ESP32PWM::allocateTimer(1);
  ESP32PWM::allocateTimer(2);
  ESP32PWM::allocateTimer(3);
  Serial.begin(115200);
  
  rearstrip.begin();           // INITIALIZE NeoPixel strip object (REQUIRED)
  rearstrip.show();            // Turn OFF all pixels ASAP
  rearstrip.setBrightness(BRIGHTNESS);

  frontstrip.begin();           // INITIALIZE NeoPixel strip object (REQUIRED)
           // Turn OFF all pixels ASAP
  frontstrip.setBrightness(LED_FRONT_BRIGHTNESS);
  

  startsequence();
  frontstrip.fill(frontstrip.Color(255,   255,   255));
   frontstrip.show();  


   indistrip.begin();
   indistrip.setBrightness(LED_INDI_BRIGHTNESS);
   indistrip.fill(frontstrip.Color(75,0,130));
   indistrip.show();


  indiindsstrip.begin();
   indiindsstrip.setBrightness(LED_INDIINSID_BRIGHTNESS);
   indiindsstrip.fill(indiindsstrip.Color(75,0,130,255));
   indiindsstrip.show();

   
  lufesppwm.attachPin(lufESPPIN, lufespfreq, 10);// 1KHz 8 bit
  luf1pwm.attachPin(luf1PIN, luf1freq, 10);// 1KHz 8 bit
  luf2pwm.attachPin(luf2PIN, luf2freq, 10);// 1KHz 8 bit

  


  Wire.onReceive(onReceive);
  Wire.onRequest(onRequest);
  Wire.begin((uint8_t)I2C_DEV_ADDR);
  #if CONFIG_IDF_TARGET_ESP32
    char message[64];
    snprintf(message, 64, "%u Packets.", i++);
    Wire.slaveWrite((uint8_t *)message, strlen(message));
  #endif


  pinMode(34, INPUT);//frontled
  pinMode(35, INPUT);//sonstwas
}

void loop() {
  

  
  


  if(millis() > stepstonextdrivespeed + lastmillisspeed){
    lastmillisspeed=millis();
    if(nextdrivespeed<=2&&nextdrivespeed>=-2){
      nextdrivespeed=0;
    }
    if(drivespeed<nextdrivespeed){
      drivespeed=drivespeed+1;
      dobreak(&rearstrip,0);
    }else if(drivespeed>nextdrivespeed){
      drivespeed=drivespeed-1;
      dobreak(&rearstrip,1);
    }else{
      stepstonextdrivespeed=1;
      dobreak(&rearstrip,0);
    }
  }
  if(millis() > stepstonextlenkung + lastmillislenkung){
    lastmillislenkung=millis();
    if(lenkung<nextlenkung){
      int add=(nextlenkung-lenkung)/10;
      lenkung=lenkung+1+add;
      //dobreak(&rearstrip,0);
      
    }else if(lenkung>nextlenkung){
      int add=(lenkung-nextlenkung)/10;
      lenkung=lenkung-1-add;
      //dobreak(&rearstrip,1);
    }else{
      stepstonextlenkung=1;
      
    }
    if(lenkung>5){
      dolinksblinken(&rearstrip,true);
      dorechtsblinken(&rearstrip,false);
    }else if(lenkung<-5){
      dolinksblinken(&rearstrip,false);
      dorechtsblinken(&rearstrip,true);
    }else{
      dolinksblinken(&rearstrip,false);
      dorechtsblinken(&rearstrip,false);
    }
  }
  
  
  updatepwm();

  

  //onupdate();

delay(2);//5
}



void startWipe(Adafruit_NeoPixel* strip,uint32_t color, long wait) {
  //if(side==0){
    //Adafruit_NeoPixel strip= rearstrip;
  //}
  /*if(ledmilli==0L){
    //ledmilli=millis();
  }*/
  strip->setPixelColor((17), color);         //  Set pixel's color (in RAM)
  strip->show();
      //delay(wait); 
     // if(millis() > ledmilli + wait){
  int p=0;
  for(int i=0; i<=6; i++) { // For each pixel in strip...
    //if(millis() > ledmilli + wait){
     // ledmilli=millis();
      strip->setPixelColor(6+i, color);         //  Set pixel's color (in RAM)
      strip->setPixelColor(5-i, color);
      strip->show(); 
    //}
      delay(wait); 
      //if(millis() > ledmilli + wait){
        //ledmilli=millis();
    strip->setPixelColor((16-i), color);         //  Set pixel's color (in RAM)
    strip->setPixelColor((18+i), color); 
      strip->show();
      p++;
      if(i>=5){
        ledmilli=0L;
      
      }
       delay(wait);  
  //}
       
  }
}
void frontstart(){
  int rangemin=0;
  int rangemax=85;
  int deltim=0;
  for(int i=0;i<2750;i++){
    int randaddr = random(rangemin, rangemax);
    int randaddg = random(rangemin, rangemax);
    int randaddb = random(rangemin, rangemax);
    
    int randled = random(0, 37);

    int r=randaddr;
    int g=randaddg;
    int b=randaddb;

    frontstrip.setPixelColor(randled, frontstrip.Color(r,   g,   b));
    frontstrip.show();

    rangemin=checkrange((i/10)-30,0,255);
    rangemax=checkrange((i/10)+85,0,255);

    deltim++;
    if(deltim>10){
      tone(luf1PIN, 3686+(i), // C
      1); // half a second
      tone(luf2PIN, 3686+(i), // C
      1);
      //delay(1); 
      deltim=0;
    }
  }
  if(digitalRead(34)==1){
    frontstrip.setBrightness(5);
  }else{
    frontstrip.setBrightness(BRIGHTNESS);
  }
  frontstrip.show();

  
}


void dobreak(Adafruit_NeoPixel* strip,int mod){
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
